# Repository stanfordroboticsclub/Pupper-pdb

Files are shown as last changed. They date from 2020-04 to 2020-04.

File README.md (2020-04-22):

# Pupper Power Distribution Board for Teensy
This is a custom power distribution board for the versions of Pupper that generate PWM signals from Teensy's that have the smaller footprint. It also has a spot to attach a Sparkfun BNO080 IMU, connected to the Teensy over I2C. 

Don't know what Pupper is? It's a cheap dynamics quadruped robot that you can build at home.
- Check out the [Project Page](https://stanfordstudentrobotics.org/pupper)
- Check out the [Code](https://github.com/stanfordroboticsclub/stanfordquadruped)

## Fabrication
1. Upload Gerbers.zip (in this directory) to the quoting mechanism on jlcpcb.com
2. It'll then give you some options on how you want the pcb made
3. Make sure you specify 2oz copper to support the high current from the servos.
4. You can leave everything else as default!

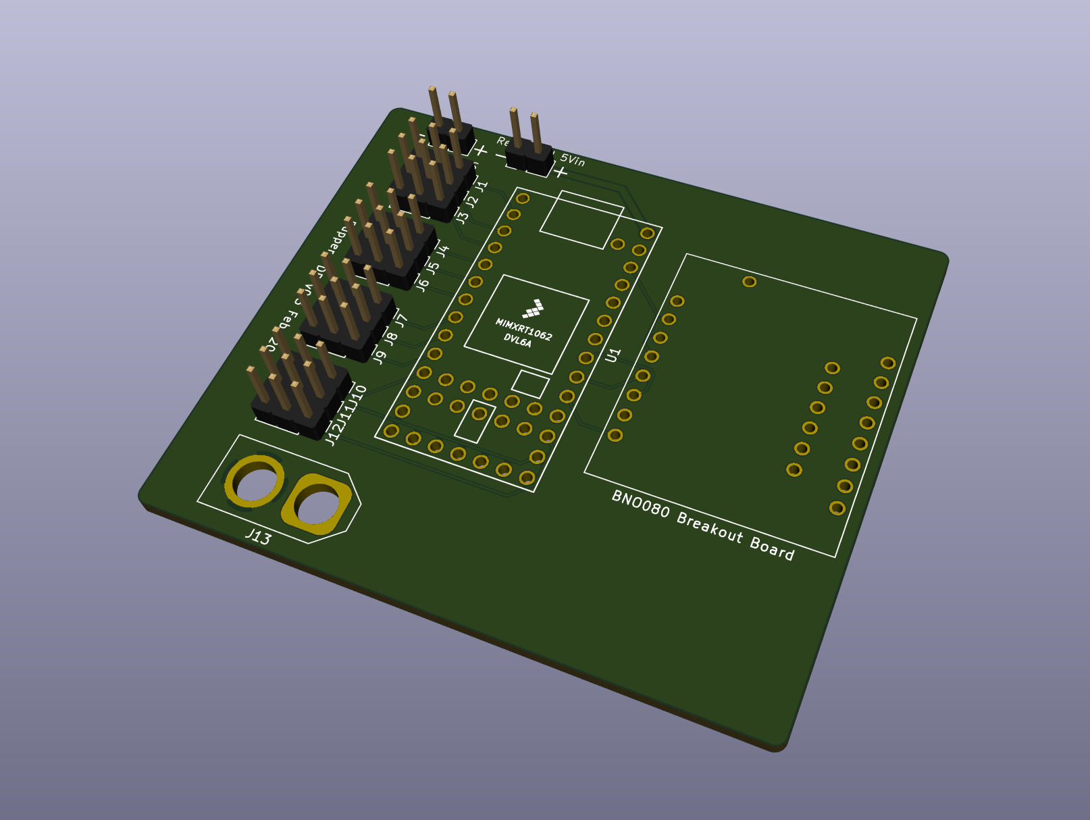
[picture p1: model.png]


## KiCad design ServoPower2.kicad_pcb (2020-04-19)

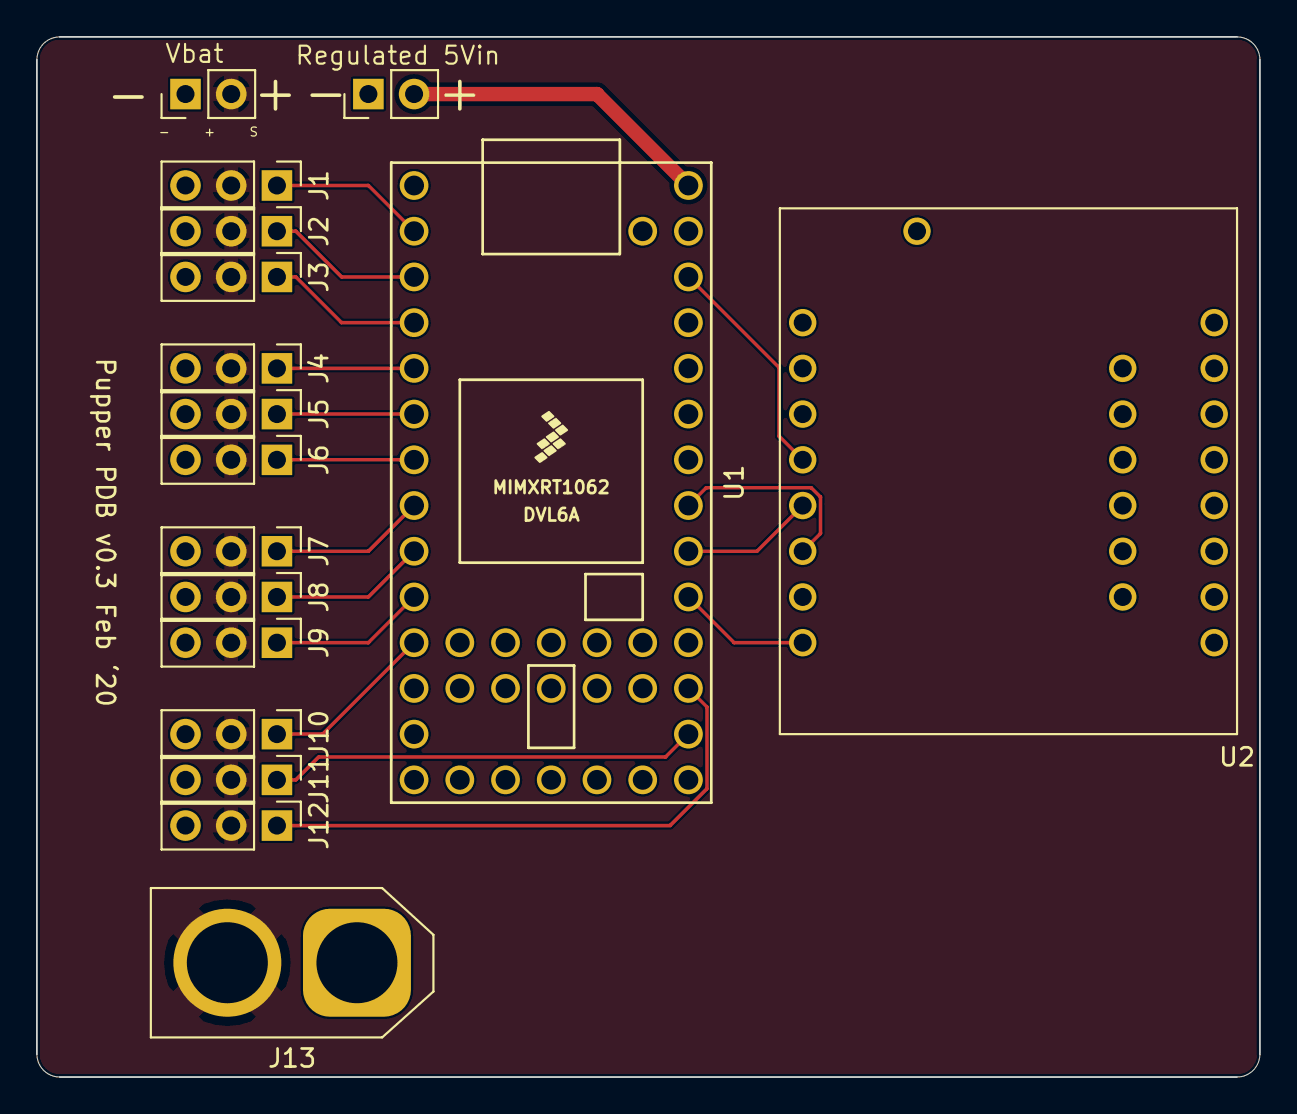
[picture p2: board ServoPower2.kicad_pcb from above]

Board: 2 copper layers, 67.9 x 57.8 mm, 17 parts (0 on the bottom side), 18 nets.

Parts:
J1, J2, J3, J4, J5, J6, J7, J8, J9, J10, J11, J12: Conn_01x03; PinHeader_1x03_P2.54mm_Vertical
J13: Conn_01x02; AMASS_XT60-M_1x02_P7.20mm_Vertical
J14, J15: Conn_01x02; PinHeader_1x02_P2.54mm_Vertical
U1: Teensy4.0; Teensy40
U2: IMUBN

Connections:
+5V: J15.2, U1.33
/INT: U1.24, U2.8
/S11: J1.1, U1.2
/S12: J2.1, U1.3
/S13: J3.1, U1.4
/S21: J4.1, U1.5
/S22: J5.1, U1.6
/S23: J6.1, U1.7
/S31: J7.1, U1.8
/S32: J8.1, U1.9
/S33: J9.1, U1.10
/S41: J10.1, U1.11
/S42: J11.1, U1.21
/S43: J12.1, U1.22
/SCL: U1.26, U2.6
/SDA: U1.25, U2.5
GND: J1.3, J2.3, J3.3, J4.3, J5.3, J6.3, J7.3, J8.3, J9.3, J10.3, J11.3, J12.3, J13.1, J14.1, J15.1, U1.1, U1.17, U1.32, U2.3
VDD: J1.2, J2.2, J3.2, J4.2, J5.2, J6.2, J7.2, J8.2, J9.2, J10.2, J11.2, J12.2, J13.2, J14.2

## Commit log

2020-04-05 clean up
    [Prelab1.kicad_pcb, Prelab1.sch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]
2020-04-18 updated to have IMU
    [ServoPower2-B_Cu.gbr, ServoPower2-B_Mask.gbr, ServoPower2-B_Paste.gbr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]
2020-04-18 added 3v3
    [ServoPower2-B_Cu.gbr, ServoPower2-B_Mask.gbr, ServoPower2-B_Paste.gbr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]
2020-04-19 Files for the IMU symbol
2020-04-19 added local dependency to imu symbol and footprint
    [ServoPower2.kicad_pcb, ServoPower2.sch]
